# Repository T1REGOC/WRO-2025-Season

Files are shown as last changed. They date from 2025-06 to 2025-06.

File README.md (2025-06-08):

# WRO-2025-Season
Respitory of the code, 3d files of the robot and some documents for the 2025 WRO Future Engineers competition from T1 REGOČ, Prigorje Brdovečko, Croatia.

About the Robot:

Introduction:

For the “Future Engineers” category, our team was given the challenge of building and programming a robot that could complete two specific tasks: the “Open Challenge” and the “Obstacle Challenge.” However, this was not just about making something that worked—we also had to follow a strict set of rules laid out in the competition guidelines. These rules covered everything from dimensions and sensors to motors and power sources. One of the most important limitations was the rule about the drive system. We couldn’t design our own custom solution from scratch. Instead, we had to choose from a set of approved drive systems listed in the rules document.
After reviewing the available options and doing research on each of them, we carefully considered which one would be the most efficient and reliable for our tasks. We eventually chose the one that best fit both challenges, and the rest of our design was built around that choice. This document explains the choices we made in terms of mechanical construction, electronics, sensors, and how the robot performs in practice.
________________________________________
Mechanical Construction and Electronics

One of the first decisions we made during the design process was about the drive system. After comparing the performance of different systems, we chose a differential drive system, which is commonly used in robotics for its simplicity and reliability. This type of system allows the robot to turn by varying the speed of the wheels on each side. Within the differential options, there are open and closed types. Open differential systems are more suitable for off-road or rough terrain. But since our robot will operate mostly on flat, indoor surfaces, we decided to use a closed differential system, which offers more stability and control.
In this setup, one TT Gear Motor is used to spin a gear, which then drives another gear connected to the wheels. This allows smooth and balanced movement. The TT Gear Motor is a compact and efficient DC motor that delivers good torque even at low voltages. Although it can run at 3V, we’ve chosen to power it using a 5V supply through an L298N motor driver to improve speed and torque. The L298N module also allows us to control the motor’s direction and speed using PWM signals.
When it came to steering our team designed a custom version of the Ackermann steering system, which is commonly used in real cars. In our design, there is a fixed base segment attached to the robot’s body. On either side of this segment, we placed two vertical pillars. Attached to these pillars are motor holders—these are the parts that actually move the wheels which are attached with a piece connecting them together. That piece, that holds them together is spun by a servo.
A SG90 servo motor is connected to this segment. When the servo turns left or right, it rotates the entire upper part of the system, causing both motor holders to turn together. This moves the front wheels in the correct direction, just like in a car. The SG90 was chosen because it is small, affordable, and operates perfectly at 5V. It is also known for its reliability.
For processing and control, we decided to utilize both the microcontroller board Arduino Uno and a Raspberry Pi 4 single-board computer. Each of them serving distinct roles within the system. The Arduino Uno is responsible for interacting with analog and real-time digital sensors, including six HC-SR04 ultrasonic distance sensors, APDS-9960 color sensor and a DHT22 temperature and humidity sensor. Its low-latency response makes it ideal for handling time-sensitive sensor readings. On the other side of our robots „brain“ we have the Raspberry Pi 4 used for high-level processing tasks, such as camera based vision processing and overall system coordination. We can compare the Raspberry Pi 4 and the Arduino Uno as the brain and nervous system. The Arduino Uno is used for sensing and reacting while the Raspberry Pi 4 is like the brain by thinking, seeing and deciding. The Raspberry Pi 4 was the perfect choice providing over 600 times the computational power of the Arduino Uno, making it perfect for demanding tasks.
To improve the accuracy of the ultrasonic readings, we added a DHT22 temperature and humidity sensor. The speed of sound can change based on air temperature and humidity, which affects the accuracy of distance readings from ultrasonic sensors. By using the data from the DHT22, we can apply corrections to the ultrasonic sensor calculations, making our readings more reliable under different conditions.
For processing and control, we decided to use a microcontroller Arduino Uno and a single board computer Raspberry Pi 4. Each of them serves a different role. The Arduino Uno is used for reading sensors that require analog inputs—something the Raspberry Pi doesn’t have. On the other hand, the Raspberry Pi 4 is here because of its processing speed and camera control. Both of these boards operate at 5V.
To power everything, we use a 3.7V 1200mAh lithium-ion battery. However, since most of our components require a 5V power supply, we use a step-up voltage regulator (S13V20F5) to convert 3.7V from the battery up to a stable 5V output. This regulator is efficient and powerful enough to handle the load from our system.



Bill of materials. 

________________________________________
Practical Use of the Robotic Solution

Now let’s talk about how the robot works in real situations. As soon as the start button is pressed, the robot begins moving forward. It looks for a colored line on the ground—either orange or blue. Depending on which color it detects first, the robot will turn left or right. Every time it crosses a colored line, a counter in the code increases. Once the counter reaches twelve, that means the robot has completed three laps around the course. At that point, the current movement code ends, and the robot either begins its parking sequence or returns to the starting area.
When the robot encounters obstacles, it uses the Raspberry Pi Camera to recognize and avoid them.
For the parallel parking task, the process is broken down into two parts: lining up and parking. First, the robot uses the two side ultrasonic sensors to make sure it is lined up perfectly parallel to the wall. It keeps adjusting until both side sensors give almost the same reading. Once the robot is aligned, it begins a classic parallel parking process, which includes moving backward at an angle, straightening out, and then moving forward to complete the parking.



Electrical Scheme

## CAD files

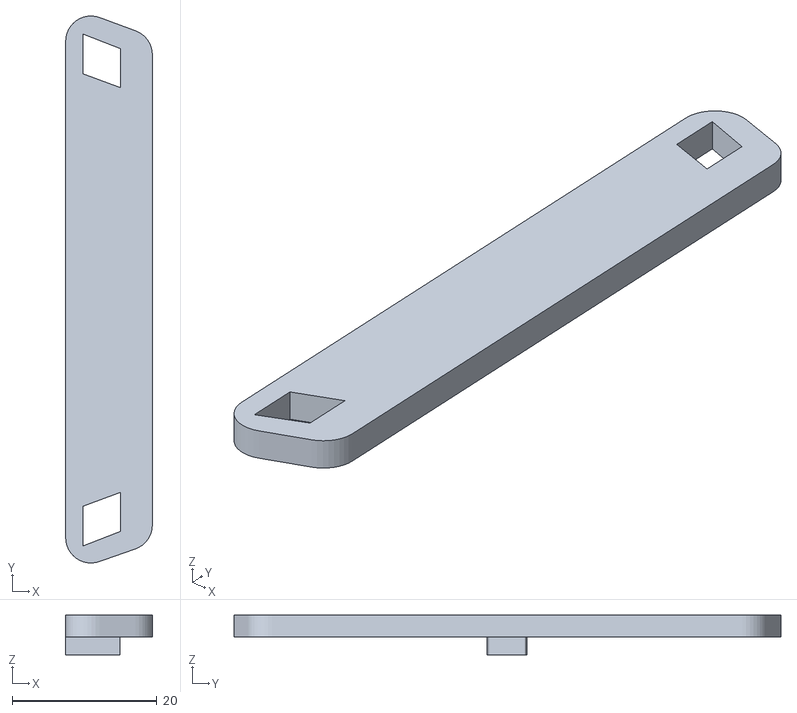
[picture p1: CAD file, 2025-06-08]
3d files/Connector.stl
12.0 x 75.7 x 5.50

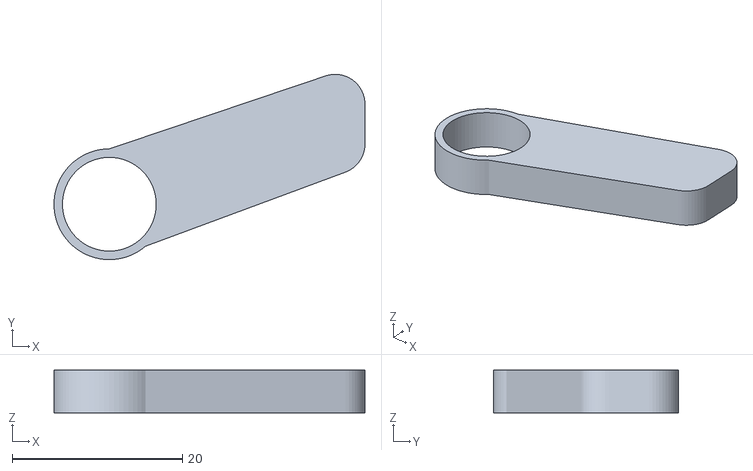
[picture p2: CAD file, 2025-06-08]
3d files/Ležaj Gornji L.stl
36.5 x 21.7 x 5.00

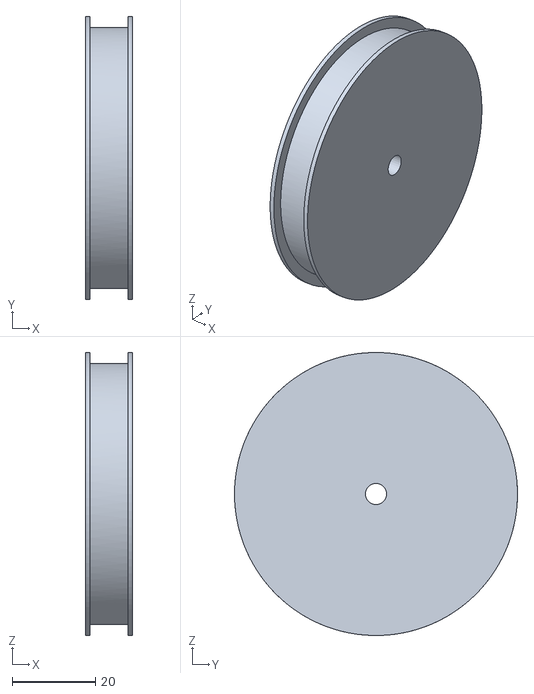
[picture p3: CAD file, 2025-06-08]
3d files/kotač frfr v5.stl
11.4 x 68.0 x 68.0

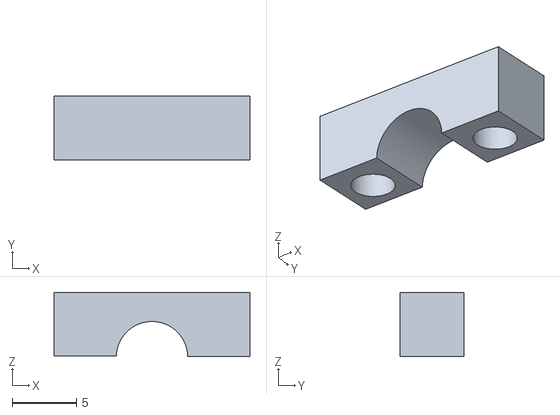
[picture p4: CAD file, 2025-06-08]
3d files/Pogon Poklopac.stl
15.3 x 5.00 x 5.00

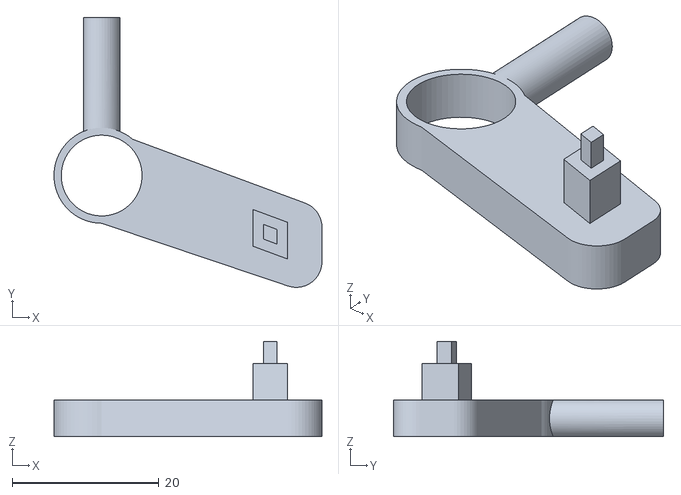
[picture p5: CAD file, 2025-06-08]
3d files/Desni ležaj.stl
36.5 x 36.7 x 13.0

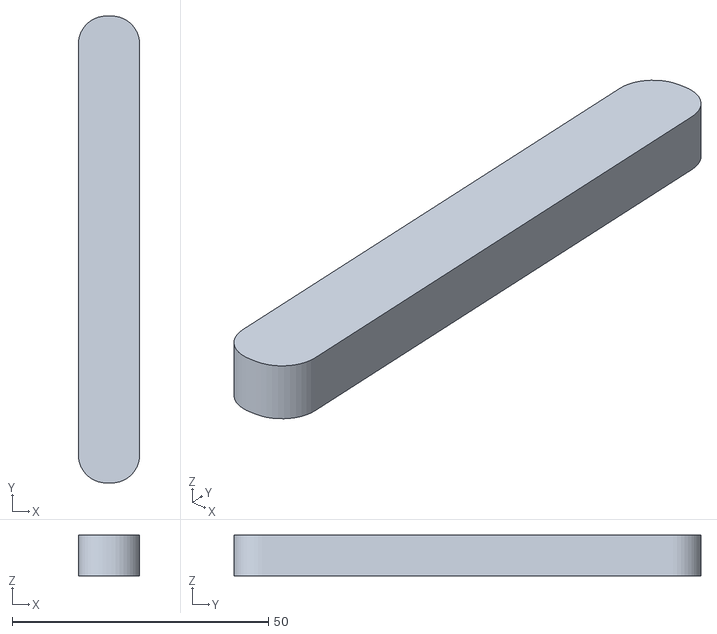
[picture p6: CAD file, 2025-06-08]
3d files/Connector Gornji.stl
12.0 x 91.2 x 8.00

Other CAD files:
3d files/Gornji Ležaj D.stl
3d files/Lijevi ležaj.stl
3d files/batteryholder.f3d
3d files/servoaddon.f3d
3d files/smallgear.f3d
3d files/wheel.f3d

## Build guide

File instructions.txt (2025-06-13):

Dht11 ima muski pinout ali zenske zice ne primaju bas tako da to mozemo ili zalemit ili nesto drugo
Dht je spojen na pin 1 iako se koristi za serial. Zato se u kodu treba samo stavit da se sa dhta cita prije pokretanja seriala(readDHT se mora stavit iznad serial.begin). Kad je kod uploadan onda se moze vratit na pin 0. Cilj je bio da ne koristimo pinove 0, 1 i 13 zato jer su 0 i 1 za serial komunikaciju koju mi koristimo, a pin 13 ima built-in LED koji ima 1k ohma resistor spojen na njega. Nazalost moramo koristiti cak 2 od ta 3 pina, koristimo pin 13 i pin 1 zato jer 0 moze pravit probleme oko seriala i uploadanja koda i svega a pin 1 je tx odnosno samo salje i on moze jedino krive podatke poslat ali s obzirom da nas program koji cita values list ne uzima u obzir informacije ako nije dostupna vrijednost od svih navedenih varijabli. 
U python skriptama treba se promjenit koje senzore koristimo. Zbog nedostatka samo jednog pina morali smo maket 1 ultrazvucni senzor zato jer njih imamo 6, a sve ostalo imamo samo po jedno. Makeli smo prednji lijevi(distance4 ili po indexu 3).
Makeli smo njega zato jer smo gledali ovako:
Prednji nam treba zato jer da nema prednjeg moze se zabit head first u zid
Zadnji nam treba za parking
Onda nam ostaju samo oni sa strana, a bitniji su nam zadnji bas zbog parkinga. Posto se u programu prije usporedivalo prosjek sad se usporeduju samo zadnji senzori.
Objašnjenje:
Ako imamo sa svake strane dva senzora i uzimamo prosjek od citanja sa neke strane mozemo to zamislit kao da uzimamo udaljenost od sredista stranice robota, a ako mi na jednoj strani imamo samo zadnji on uzima ocitanja sa zadnje strane robota, a ako usporedujemo to sa prosjekom senzora onda bi mi u prevedenom na jednoj strani gledali kolika je udaljenost izmedu zadnjeg senzora i zida, a na drugoj udaljenost izmedu polovice strane robota i zida sto nije isto 
Duljina linije boje na mapi je na kutu od 90 stupnjeva 5cm. Preko toga se moze dobit delay ako imamo brzinu.
Delay na arduino programu se moze smanjit ako robot to dozvoljava
A1 i A2 mogu bit invertirani.
+ i - od ls motor drivera mora biti na power supplyu direktno, a A1 i A2 oviseci koji koristimo za high umjesto high stavljamo pwm
Open challenge: koristi se samo arduino, a ne i raspberry. On radi tako da u setupu izracuna speed of sound i blue_count i orange_count se postavlja na 0 i u loopu stavlja se motorpower na max i postavlja se smjer motora i onda se pokrece while petlja sa uvjetom dok je blue_count ili orange_count manje od 12. Nakon toga postavljam motorpower na 0. Napomena: kad se while zavrsi onda se loopaju max power i 0

U kodovima se mora promjenit:
pinout(pise na raspberry u pinout.txt) !!DHT se prebacuje sa 0 na 1
Provjerit kad se usporeduju udaljenosti(mainly WRO_Logic) moraju se usporedivat samo zadnji, a ne prosjek dvaju senzora
Raspberry pi GPIO su svi stavljeni na Board number(pin 1 je pin 1), a ne BCM
Svi trigPinovi od ultrazvucnih su spojeni na isti arduino pin
values list ide ovako
values = [distance1, distance2, distance3, distance4, distance5, distance6, way, blue_count, orange_count]

SerialWRO cita serial sa arduina i kreira values list
WRO_logic radi navigaciju i sve ostalo, na kraju programa pisu funkcije 

od WRO_logica je testiran dio za kameru gdje detektira kako treba vanjske tocke i korektno definira smjer skretanja

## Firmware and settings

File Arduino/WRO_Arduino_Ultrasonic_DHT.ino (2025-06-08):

#include <DHT11.h>  // Include the DHT sensor library to read temperature and humidity data.
#include <NewPing.h>  // Include the NewPing library to control ultrasonic sensors.
#include <Wire.h>
#include <Servo.h>

#define APDS9960_ADDR 0x39 // I2C address for the APDS9960 sensor.
#define ENABLE_REG 0x80 // Register address for enabling the APDS9960 sensor.
#define ATIME_REG 0x81 // Register address for the APDS9960 sensor's integration time.
#define CONTROL_REG 0x8F // Register address for controlling the APDS9960 sensors gain and other settings.
#define CDATAL_REG 0x94 // Register address for reading color data from the APDS9960 sensor.
#define trigPin 2  // The trigger pin for all the ultrasonic sensors (sending the pulse).
#define echoPin1 3  // The echo pin for the first ultrasonic sensor.
#define echoPin2 5  // The echo pin for the second ultrasonic sensor.
#define echoPin3 6  // The echo pin for the third ultrasonic sensor.
#define echoPin4 7  // The echo pin for the fourth ultrasonic sensor.
#define echoPin5 8  // The echo pin for the fifth ultrasonic sensor.
#define echoPin6 9  // The echo pin for the sixth ultrasonic sensor.
#define dhtPin 4  // The data pin for the DHT22 sensor.
#define maximum 400  // Maximum range of the ultrasonic sensors in cm.

DHT11 dht11(4); // Initialize the DHT11 sensor object on pin 4.

Servo stmotor;
//steering motors for detection
#define m1 12
#define m2 A0
#define m3 A1
#define m4 A2

//speed motors
#define s1 10
#define s2 11

// power pins for speed
#define p A3

NewPing sonar1(trigPin, echoPin1, maximum);  // Initialize the first ultrasonic sensor.
NewPing sonar2(trigPin, echoPin2, maximum);  // Initialize the second ultrasonic sensor.
NewPing sonar3(trigPin, echoPin3, maximum);  // Initialize the third ultrasonic sensor.
NewPing sonar4(trigPin, echoPin4, maximum);  // Initialize the fourth ultrasonic sensor.
NewPing sonar5(trigPin, echoPin5, maximum);  // Initialize the fifth ultrasonic sensor.
NewPing sonar6(trigPin, echoPin6, maximum);  // Initialize the sixth ultrasonic sensor.

int readDHT, temp, hum, SoS;  // Variables for reading temperature and humidity, and calculating speed of sound.
float duration1, duration2, duration3, duration4, duration5, duration6;  // Variables to store the pulse duration from each ultrasonic sensor.
float distance1, distance2, distance3, distance4, distance5, distance6;  // Variables to store the calculated distance from each sensor.
int prev_r = 0, prev_g = 0, prev_b = 0; // Previous detected colors

void setup() {
  Serial.begin(9600);  // Start serial communication for debugging and output.

  Wire.begin(); // Initialize I2C communication.

  apds_write(ENABLE_REG, 0b00000011); // Enable the APDS9960 sensor.
  apds_write(ATIME_REG, 0xDB); // Set the integration time for the APDS9960 sensor.
  apds_write(CONTROL_REG, 0x01); // Set the gain for the APDS9960 sensor.
  // Read data from the DHT22 sensor.
  readDHT = dht11.readTemperatureAndHumidity(temp, hum);  
  
  // Calculate the speed of sound based on temperature and humidity using the formula.
  SoS = 331.4 + (0.6 * temp) + (0.0124 * hum);

}

void loop() {
  delay(120);

  uint16_t c = read16(CDATAL_REG); // Read the color data from the APDS9960 sensor.
  uint16_t r= read16(CDATAL_REG + 2); // Read the red color data.
  uint16_t g= read16(CDATAL_REG + 4); // Read the green color data.
  uint16_t b= read16(CDATAL_REG + 6); // Read the blue color data.

  int r255 = (c > 0) ? constrain((float)r / c * 255, 0, 255) : 0; // Convert the red color data to a value between 0 and 255.
  int g255 = (c > 0) ? constrain((float)g / c * 255, 0, 255) : 0; // Convert the green color data to a value between 0 and 255.
  int b255 = (c > 0) ? constrain((float)b / c * 255, 0, 255) : 0; // Convert the blue color data to a value between 0 and 255.

  int diff = abs(r255 - prev_r) + abs(g255 - prev_g) + abs(b255 - prev_b); // Calculate the difference in color values to detect significant changes.
  
  // Get the pulse duration from the first ultrasonic sensor and convert it to seconds.
  duration1 = sonar1.ping_median(2);  // Use median of 2 pings to avoid .
  duration1 = duration1 / 1000000;  // Convert microseconds to seconds.
  
  // Calculate the distance using the formula: distance = (speed of sound * duration) / 2.
  distance1 = (SoS * duration1) / 2;

  // Repeat the process for the other five ultrasonic sensors.
  duration2 = sonar2.ping_median(2);
  duration2 = duration2 / 1000000;
  distance2 = (SoS * duration2) / 2;
  
  duration3 = sonar3.ping_median(2);
  duration3 = duration3 / 1000000;
  distance3 = (SoS * duration3) / 2;
  
  duration4 = sonar4.ping_median(2);
  duration4 = duration4 / 1000000;
  distance4 = (SoS * duration4) / 2;
  
  duration5 = sonar5.ping_median(2);
  duration5 = duration5 / 1000000;
  distance5 = (SoS * duration5) / 2;
  
  duration6 = sonar6.ping_median(2);
  duration6 = duration6 / 1000000;
  distance6 = (SoS * duration6) / 2;

  if (diff > 60) { // Only check color if a big change happened
    if (b255 > 120 && r255 < 80 && g255 < 100) {
      Serial.println(String(distance1) + "," + String(distance2) + "," + String(distance3) + "," + String(distance4) + "," + String(distance5) + "," + String(distance6) + "b");
    } else if (r255 > 140 && g255 > 60 && g255 < 160 && b255 < 80) {
      Serial.println(String(distance1) + "," + String(distance2) + "," + String(distance3) + "," + String(distance4) + "," + String(distance5) + "," + String(distance6) + "o");
    } else {
      Serial.println(String(distance1) + "," + String(distance2) + "," + String(distance3) + "," + String(distance4) + "," + String(distance5) + "," + String(distance6) + "w");
    }
  }

  prev_r = r255;
  prev_g = g255;
  prev_b = b255;

  speed();
  if (speed != prev_speed){ // Check if speed has changed
    switch(speed){
      case "01":
        analogWrite(p, 64); // Set speed to 25%
        break;
      
      case "10":
        analogWrite(p, 128); // Set speed to 50%
        break;
      
      case "11":
        analogWrite(p, 255); // Set speed to 100%
        break;
    }
  }

  steering();
  if (steering != prev_steering){ // Check if steering has changed
    switch(steering){
      case "0000":
        //off
        break;

      case "0001":
        //l(low)
        stmotor(75); // Set steering motor to low left
        break;

      case "0010":
        //l(mid)
        stmotor(60); // Set steering motor to mid left
        break;

      case "0011":
        //l(full)
        stmotor(45); // Set steering motor to full left
        break;

      case "0100":
        //s(straight)
        stmotor(90); // Set steering motor to straight
        break;

      case "0101":
        //r(low)
        stmotor(105); // Set steering motor to low right
        break;

      case "0110":
        //r(mid)
        stmotor(120); // Set steering motor to mid right
        break;

      case "0111":
        //r(full)
        stmotor(135); // Set steering motor to full right
        break;
    }

  }
  prev_speed = speed; 
  prev_steering = steering;
}

void apds_write(uint8_t reg, uint8_t value) { // Function to write a value to a specific register of the APDS9960 sensor.
  Wire.beginTransmission(APDS9960_ADDR); // Start I2C transmission to the APDS9960 sensor.
  Wire.write(reg); // Write the register address.
  Wire.write(value); // Write the value to the register.
  Wire.endTransmission(); // End the I2C transmission.
}

void speed(){
  if (analogRead(s1) > 40){
    s1 = 1; // If the analog reading from s1 is greater than 40, set s1 to 1.
  }
  if (analogRead(s2) > 40){
    s2 = 1; // If the analog reading from s2 is greater than 40, set s2 to 1.
  }
  speed = String(String(m1) + String(m2)); // Combine the values of s1 and s2 to form the speed string.
  return speed
}

void steering(){
  if(analogRead(m1) > 40){
    m1 = 1; // If the analog reading from m1 is greater than 40, set m1 to 1.
  }
  if(analogRead(m2) > 40){
    m2 = 1; // If the analog reading from m2 is greater than 40, set m2 to 1.
  }
  if(analogRead(m3) > 40){
    m3 = 1; // If the analog reading from m3 is greater than 40, set m3 to 1.
  }
  if(analogRead(m4) > 40){
    m4 = 1; // If the analog reading from m4 is greater than 40, set m4 to 1.
  }
  steering = String(String(m1)+String(m2)+String(m3)+String(m4)); // Combine the values of m1, m2, m3, and m4 to form the steering string.
  return steering
}

uint16_t read16(uint8_t reg) { // Function to read a 16-bit value from a specific register of the APDS9960 sensor.
  Wire.beginTransmission(APDS9960_ADDR); // Start I2C transmission to the APDS9960 sensor.
  Wire.write(0x80 | reg); // Write the register address with the read command bit set.
  Wire.endTransmission(false); // End the transmission but keep the connection open for reading.
  Wire.requestFrom(APDS9960_ADDR, 2); // Request 2 bytes of data from the sensor.
  if (Wire.available() < 2) return 0; // If less than 2 bytes are available, return 0 (error).
  uint8_t lsb = Wire.read(); // Read the least significant byte.
  uint8_t msb = Wire.read(); // Read the most significant byte.
  return ((uint16_t)msb << 8) | lsb; // Combine the two bytes into a 16-bit value and return it.
}

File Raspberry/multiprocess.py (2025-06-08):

import multiprocessing # Importing the multiprocessing module
import WRO_logic # Importing the WRO_logic module for the main logic of the program
import SerialWRO # Importing the SerialWRO module for serial communication

if __name__ == "__main__": 
    manager = multiprocessing.Manager() # Creating a manager to handle shared data between processes
    values = manager.list([0, 0, 0, 0, 0, 0, '', 0, 0])  # Shared list for sensor values
                # sensor1, sensor2, sensor3, sensor4, sensor5, sensor6, way, blue(count), orange(count)
    p1 = multiprocessing.Process(target=WRO_logic.main, args=(values,)) # Main logic process
    p2 = multiprocessing.Process(target=SerialWRO.serial_reader, args=(values,)) # Serial reader process

    p1.start() # Starting the main logic process
    p2.start() # Starting the serial reader process

    p1.join() # Waiting for the main logic process to finish
    p2.join() # Waiting for the serial reader process to finish
